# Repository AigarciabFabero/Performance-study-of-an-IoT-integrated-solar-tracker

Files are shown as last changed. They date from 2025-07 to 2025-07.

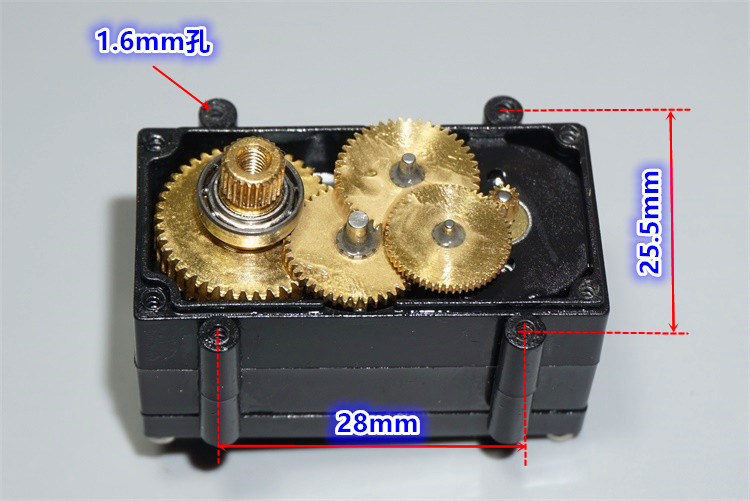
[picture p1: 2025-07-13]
Segunda_Parte/Print3D/movil/medidas/medidas3.jpg

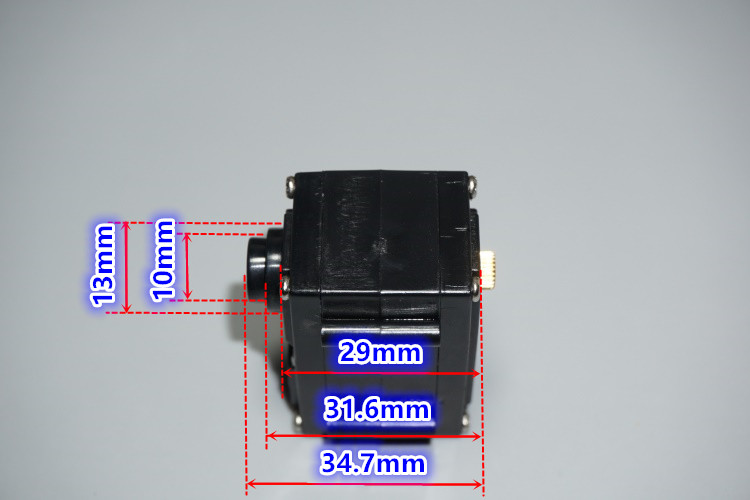
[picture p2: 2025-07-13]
Segunda_Parte/Print3D/movil/medidas/medidas1.jpg

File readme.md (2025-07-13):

# [Desarrollo y estudio del rendimiento de un seguidor solar astronómico integrado en IoT](https://dehesa.unex.es:8443/handle/10662/16877)

## Resumen

Con el objeto de mejorar la producción fotovoltaica, se pretende estudiar el rendi-
miento que se obtiene al emplear un seguidor Solar astronómico de dos ejes, respecto
a un panel fijo.
Para ello, se diseña y fabrica un prototipo constituido por dos células policristalinas
de silicio. Una de ellas sobre una estructura fija y la otra sobre un seguidor Solar
fundamentado en ecuaciones de Astrofísica y controlado por dos servomotores de tipo
bus. Además, para estudiar la mejora en la producción fotovoltaica, se diseña para
este trabajo una carga activa controlada por microcontrolador, que permite obtener el
punto de máxima potencia en todo instante.
Los datos obtenidos se suben a una plataforma de Internet de las cosas (IoT), para
su posterior estudio estadístico.
En todos los escenarios se ha podido comprobar como el seguidor Solar astronómico
de dos ejes proporciona una mejora significativa del rendimiento frente a un panel fijo
o un eje móvil.

## Abstract

The End-of-Degree Project (EDP) aims to study the improvement in photovoltaic
production achieved with a two-axis Solar tracker with respect to a fixed panel. To this
end, a prototype will be designed and built consisting of two small Solar panels, one
of them fixed and the other on a two-axis tracker controlled by bus-type servos. To
study the energy production, each panel will be connected to an active load, designed
for this work, and controlled by a microcontroller.
The data obtained will be uploaded to an Internet of Things (IoT) plataform for
forther statistical study.
In all scenarios, it has been demonstrated how the two-axis astronomical Solar
tracker provides a significant performance improvement compared to a fixed panel or
a single mobile axis.

## Prototipo final

<p align="center">
  video
</p>

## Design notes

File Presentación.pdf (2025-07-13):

### Departamento de Ingeniería Eléctrica, Electrónica y Automática

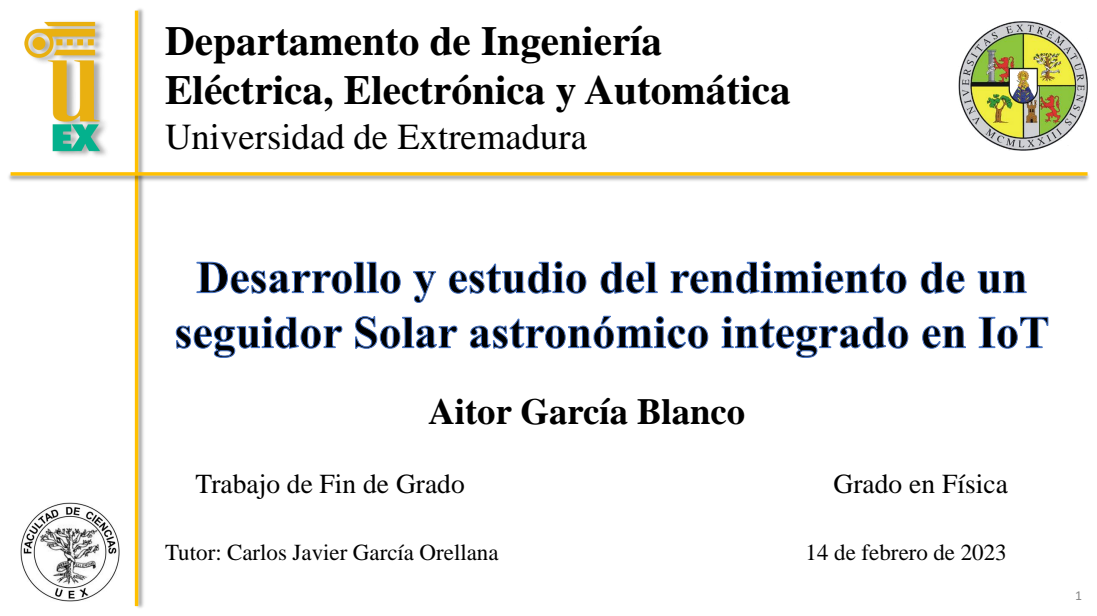
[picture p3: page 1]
Tutor: Carlos Javier García Orellana; 14 de febrero de 2023; Trabajo de Fin de Grado; Grado en Física

Universidad de Extremadura

Aitor García Blanco

## Índice

1. Introducción
2. Antecedentes
3. Materiales y desarrollo
4. Resultados ▪ Carga activa ▪ Seguidor Solar
5. Conclusiones

2

Índice

## Introducción

3

## Introducción

Con el objeto de mejorar la producción fotovoltaica, se estudia el rendimiento de un seguidor Solar astronómico de dos ejes frente a una posición fija.
- Desarrollo de una carga activa.
- Diseñar y fabricar la estructura mecánica del seguidor.
- Subir periódicamente los datos a la plataforma de “Internet of Things” (IoT).
- Analizar y estudiar los resultados obtenidos.
Introducción | 4

## Antecedentes

5

## Seguidor Solar

Estructuras móviles que pretenden maximizar la producción de electricidad en instalaciones fotovoltaicas.
➢Seguidores Solares de un único eje móvil
➢Seguidor de dos ejes móviles:
➢Control manual
➢Control automático:
➢Emplean sensores fotosensibles
➢Se fundamentan en ecuaciones astronómicas
Antecedentes | 6

## Astrofísica – Radiación Solar

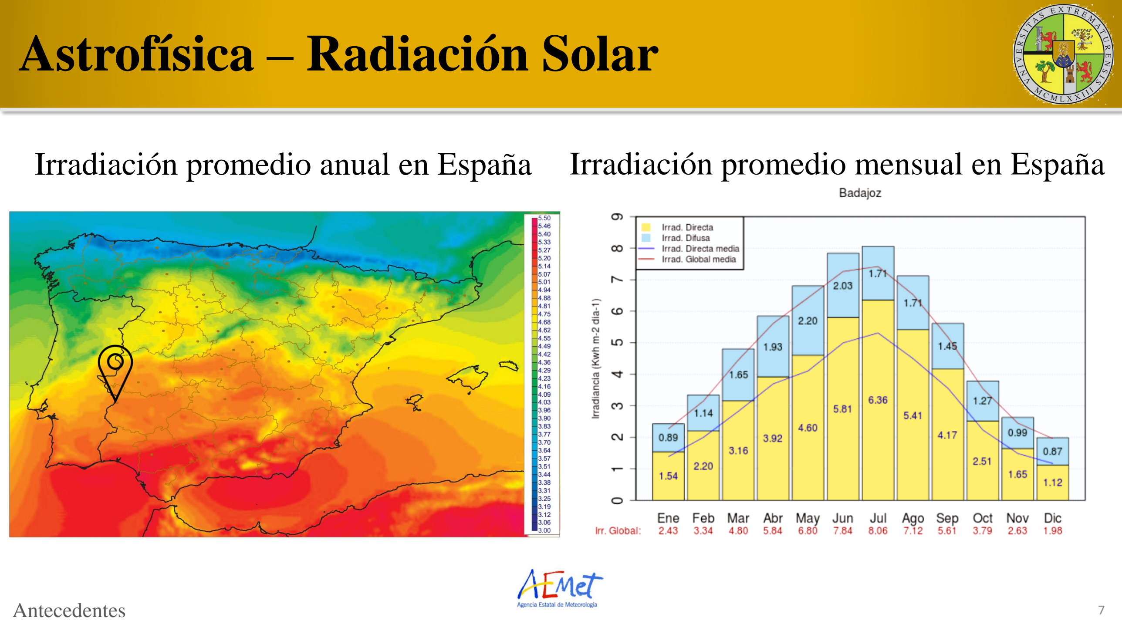
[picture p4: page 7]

Antecedentes | 7
Irradiación promedio anual en España | Irradiación promedio mensual en España

## Astrofísica – Astronomía esférica

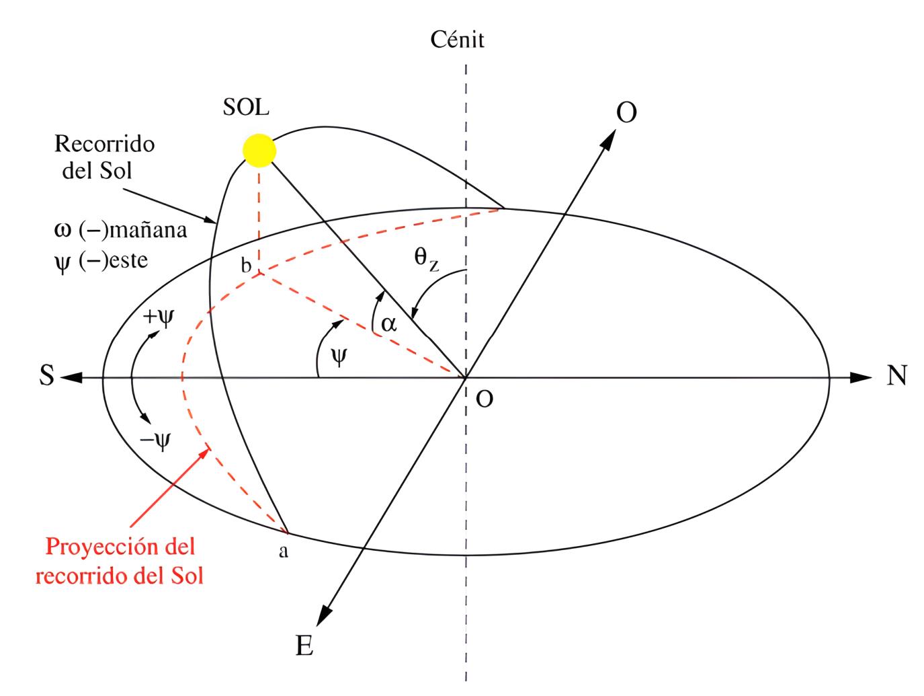
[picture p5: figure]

Antecedentes | 8

## Energía Solar fotovoltaica

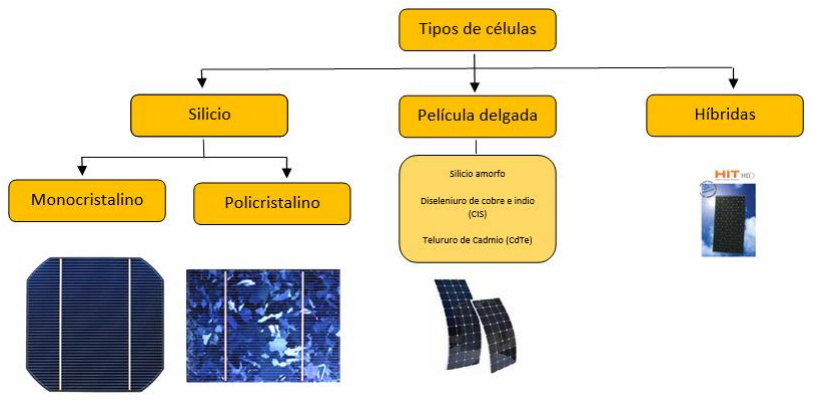
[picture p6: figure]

Antecedentes | 9

## Energía Solar fotovoltaica

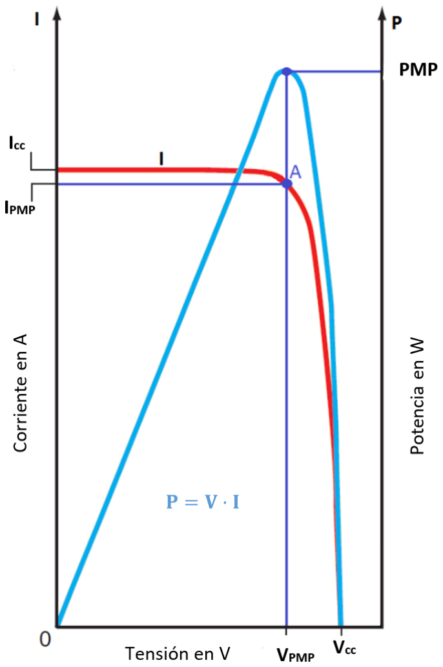
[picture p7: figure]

Antecedentes | 10

## Energía Solar fotovoltaica

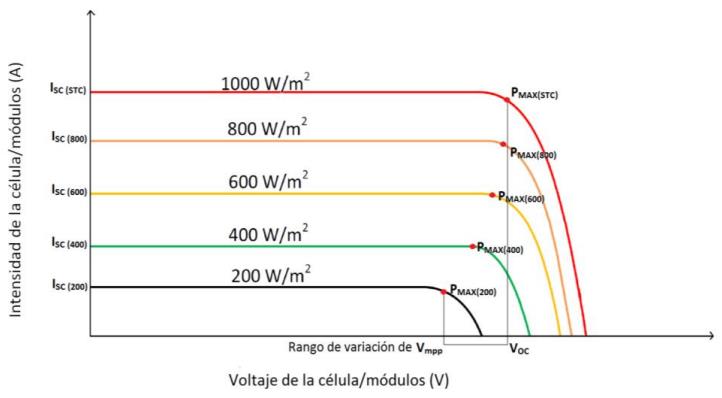
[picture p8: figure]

Antecedentes | 11

## Energía Solar fotovoltaica

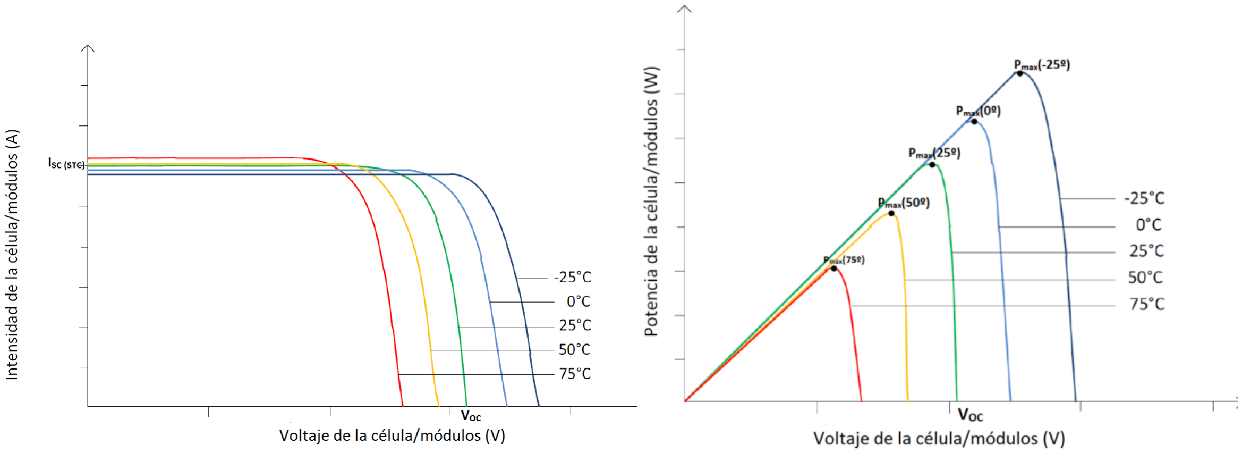
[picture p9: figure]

Antecedentes | 12

## Materiales y desarrollo

13

## Materiales

14

❑Microcontrolador ESP32

Materiales y desarrollo

❑ Células fotovoltaicas

❑ MOSFET ❑ Servomotores

❑ Conversor DC-DC

❑ Arduino IDE ❑ OpenSCAD

❑ Componentes activos y pasivos

❑ ThingSpeak

## Carga Activa - Hardware

Materiales y desarrollo | 15
- Es un dispositivo electrónico que nos permite variar la corriente que se demanda a una fuente de tensión o batería
- En este trabajo se emplea para obtener el punto de máxima potencia de la célula Solar controlando el setpoint de la corriente; siendo así, un elemento fundamental del proyecto.
- Se ha diseñado explícitamente para este trabajo

## Carga Activa - Hardware

Materiales y desarrollo | 16

## Carga activa - Hardware

17

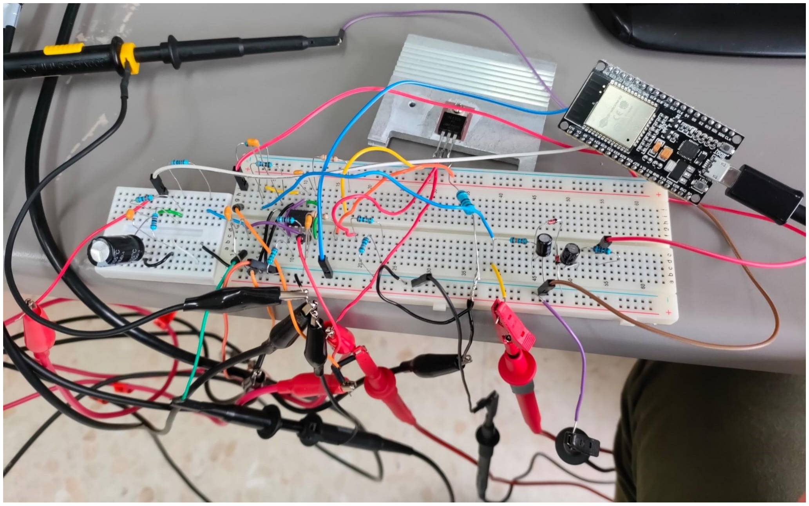
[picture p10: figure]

## Carga Activa - Software

18

- Regula la salida del DAC para mantener el setpoint para la corriente
- Incluye un lazo de control PI y un filtro de mediana para las entradas del ADC
- Para encontrar el punto de máxima potencia, el software hace un muestreo por aproximaciones sucesivas variando el setpoint de la corriente
- Una vez se encuentra el punto máximo, se repite para la otra célula fotovoltaica

Materiales y desarrollo

## Comparación rendimiento células solares

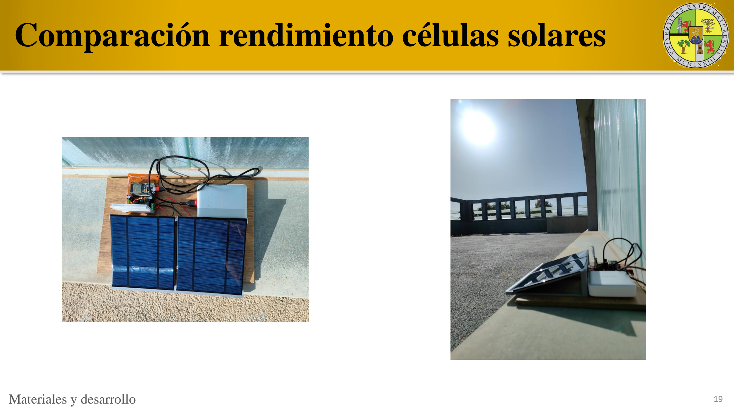
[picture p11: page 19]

Materiales y desarrollo | 19

## Comparación rendimiento células solares

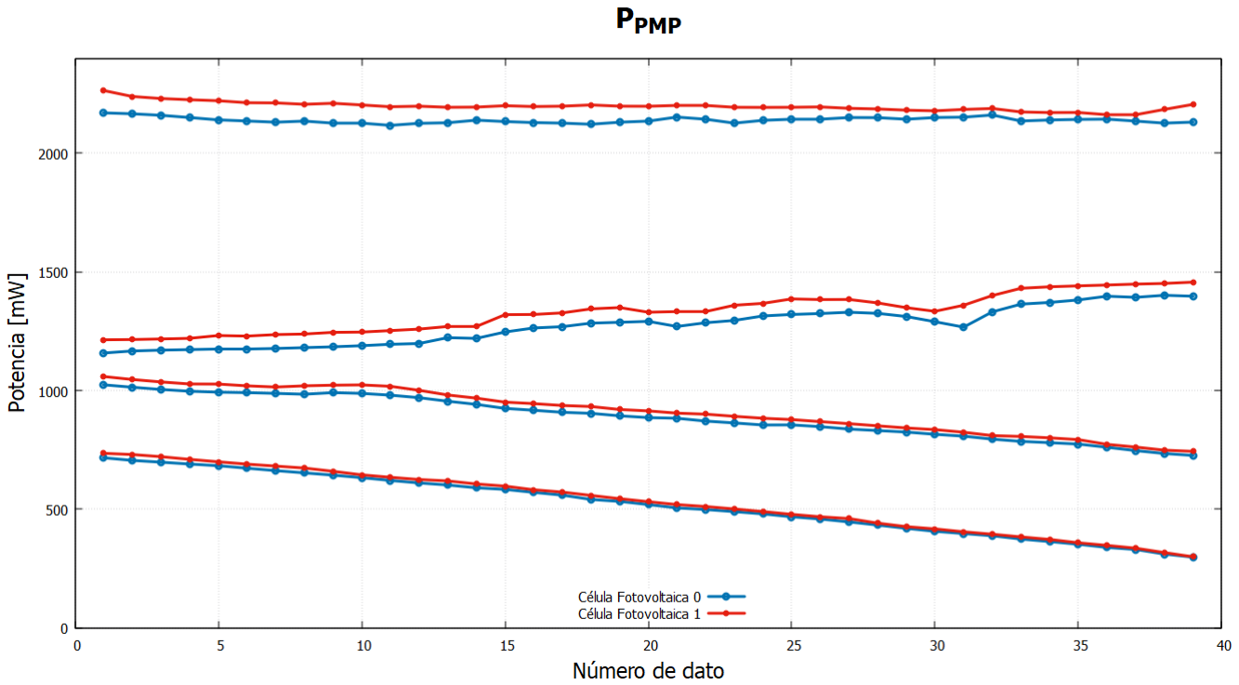
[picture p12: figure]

Materiales y desarrollo | 20

## Seguidor – Impresión 3D

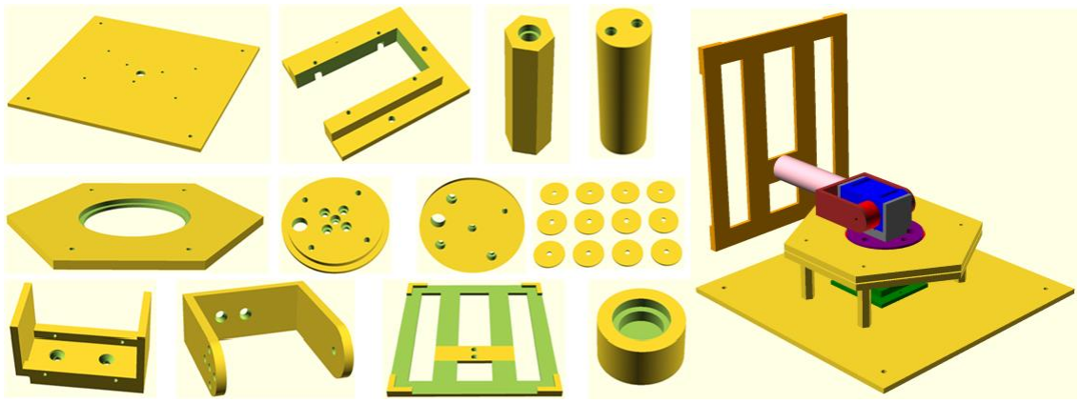
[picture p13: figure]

Materiales y desarrollo | 21

## Seguidor – Impresión 3D

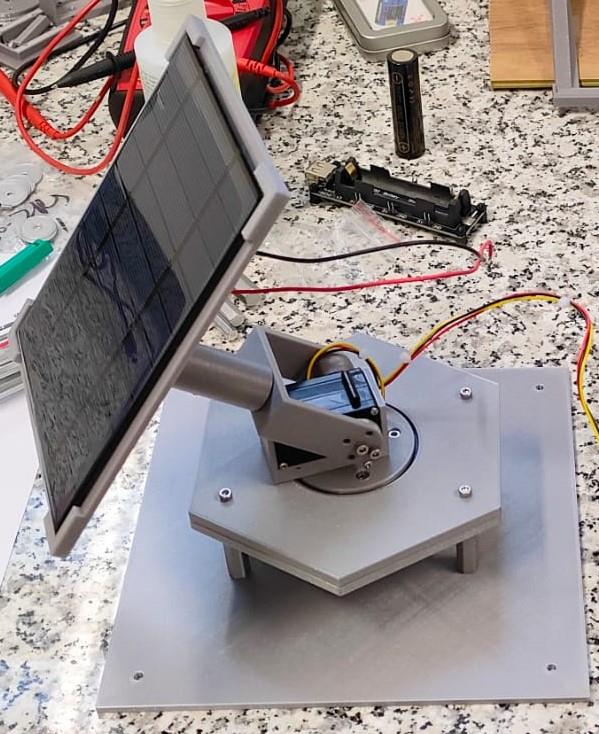
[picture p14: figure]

Materiales y desarrollo | 22

## Seguidor – Software

23

- Biblioteca de tiempos (ESP32Time) sincroniza con el servidor NTP (Network Time Protocol) , para proporciona información de tiempo en España
- Con la finalidad de obtener α y ψ, se emplean los Cálculos Generales de Posición Solar publicados por NOAA (National Oceanic and Atmospheric Administration)
- El cero del servomotor es 120 y el rango de movimiento [0-240]
- El movimiento del servo de dos ejes, tan solo tiene lugar cuando α ≥ 0

Materiales y desarrollo

## Integración

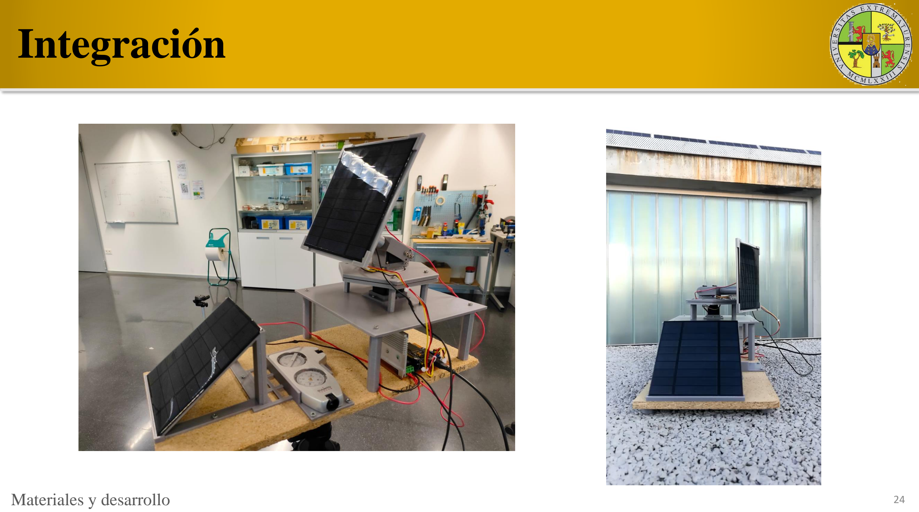
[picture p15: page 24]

Materiales y desarrollo | 24

## Integración

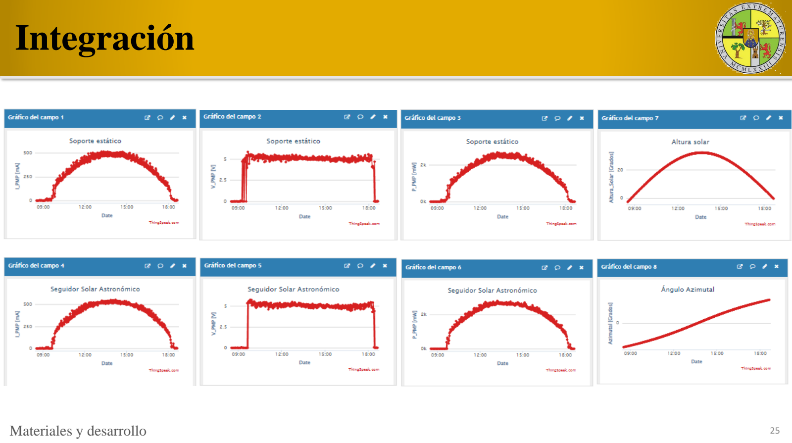
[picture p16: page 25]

Materiales y desarrollo | 25

## Resultados

26

## Carga Activa

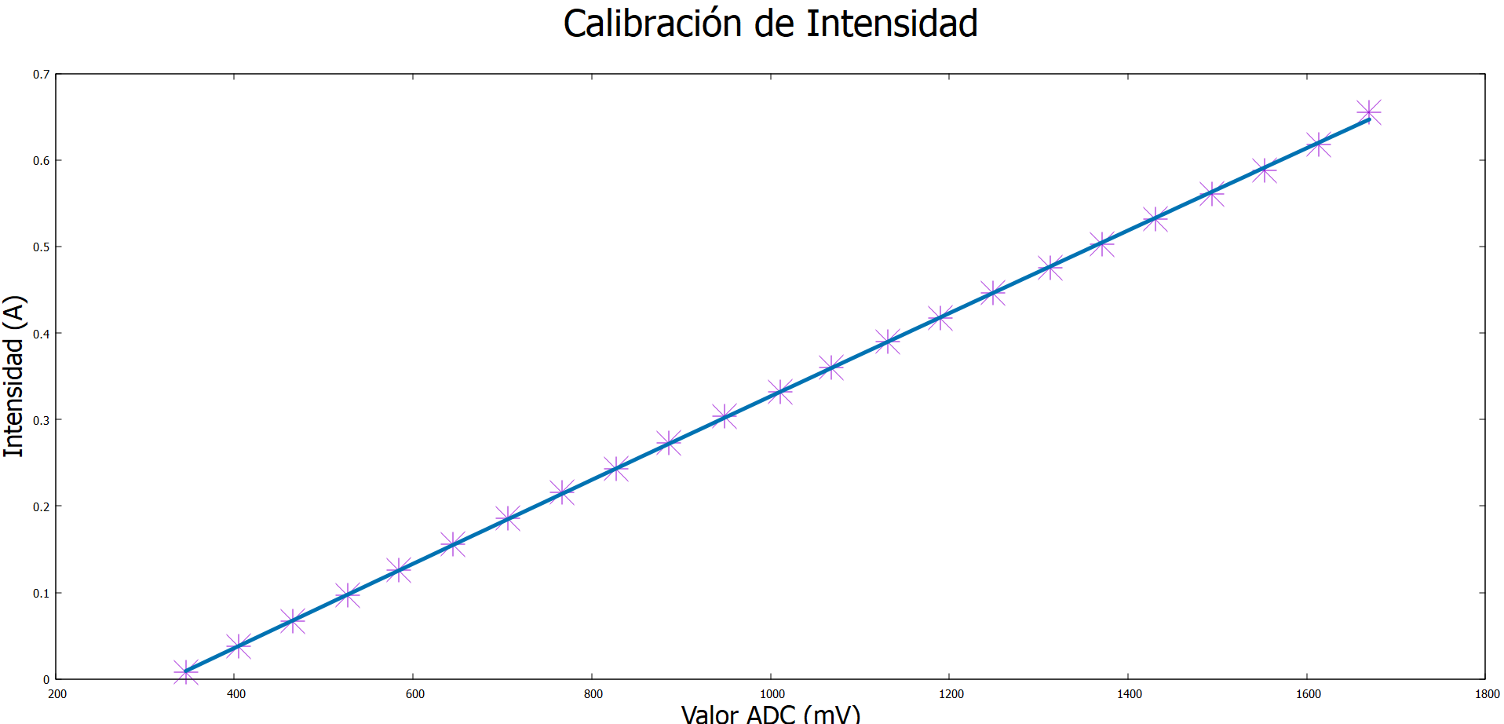
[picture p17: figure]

Resultados | 27

## Carga Activa

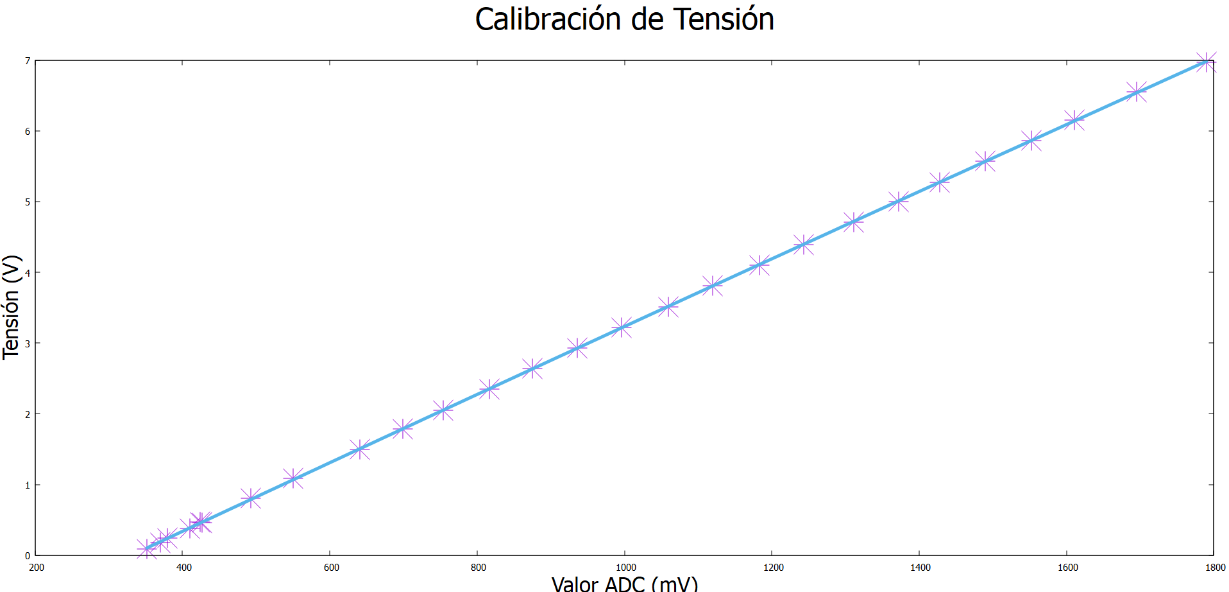
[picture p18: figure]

Resultados | 28

## Carga Activa

Resultados | 29
Calibración de la intensidad | Calibración de la tensión
a = (-5,581 ± 3,426)10⁻⁹ | a = (-5,793 ± 1,153)10⁻⁸
b = (4,933 ± 0,070)10⁻⁴ | b = (-5,581 ± 3,430)10⁻³
c = -0,160 ± 0,003 | c = -1,622 ± 0,010
R² = 0,999 | R² = 0,999

f x = ax

2 + bx + c

## Seguidor Solar

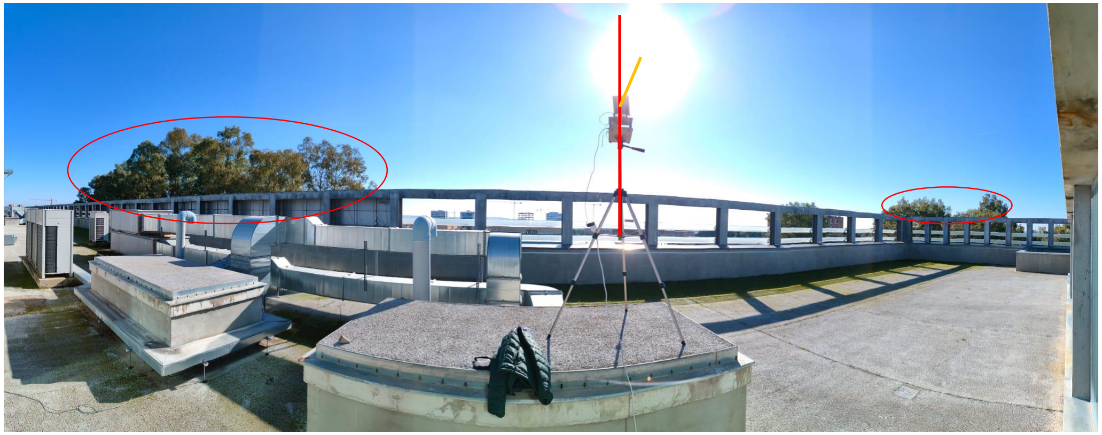
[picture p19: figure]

Resultados | 30

## Eje vertical móvil

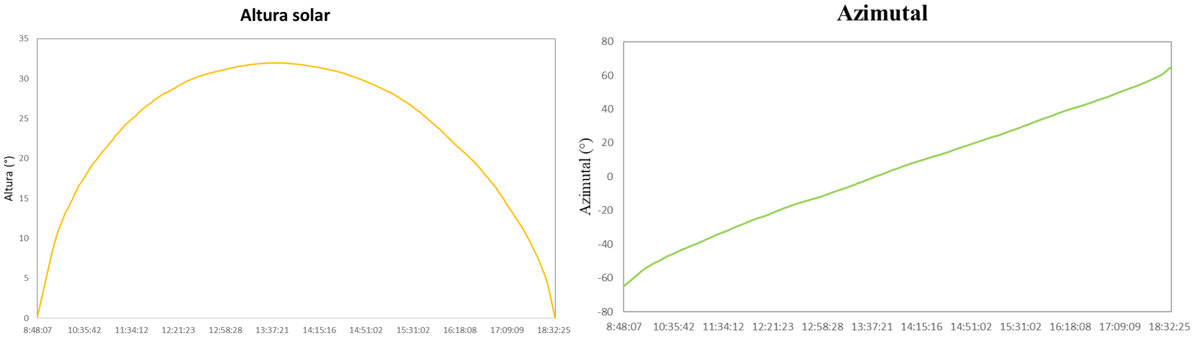
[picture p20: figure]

Resultados | 31

## Eje vertical móvil

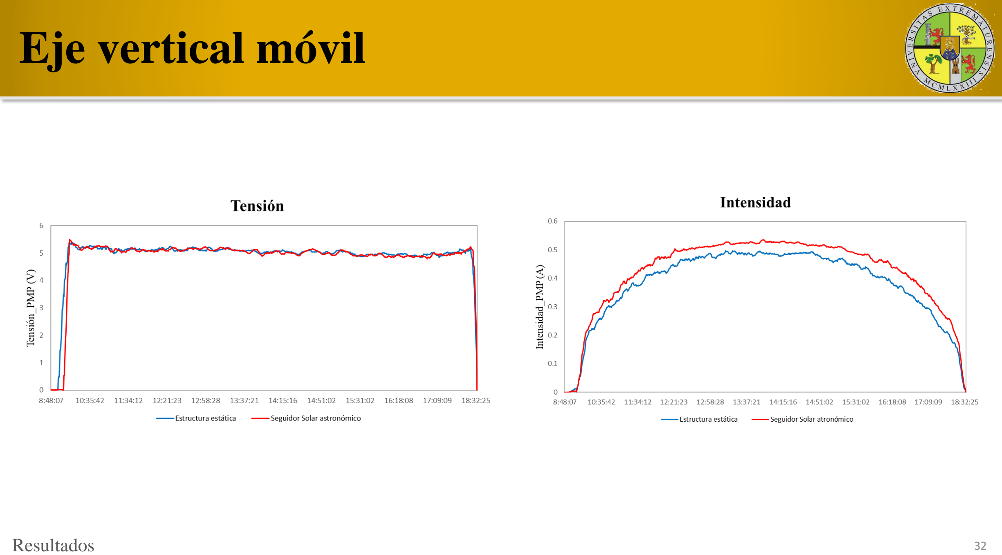
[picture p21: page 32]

Resultados | 32

## Eje vertical móvil

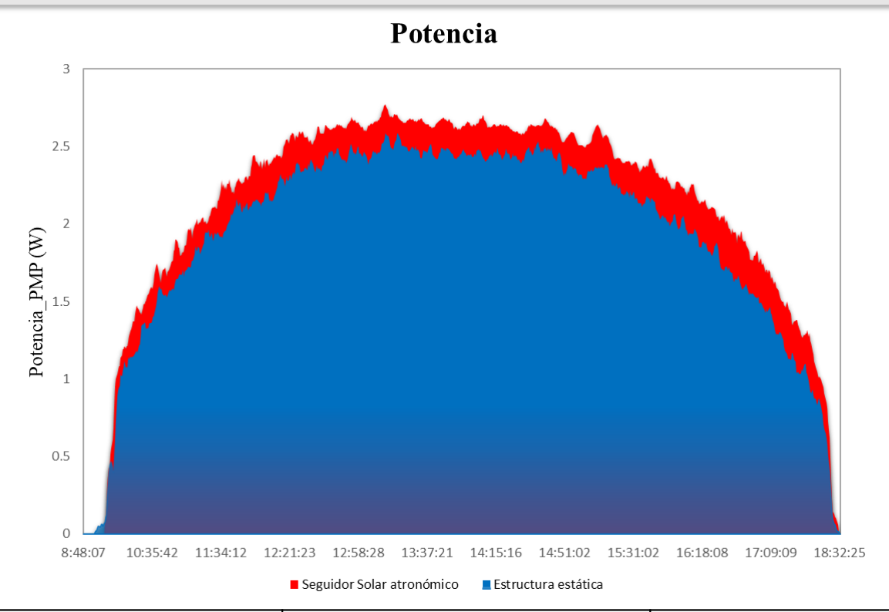
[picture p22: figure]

Resultados | 33
Energía fijo | Energía seguidor | Mejora del rendimiento
15,95 Wh | 17,71 Wh | 11,03 %

## Eje horizontal móvil

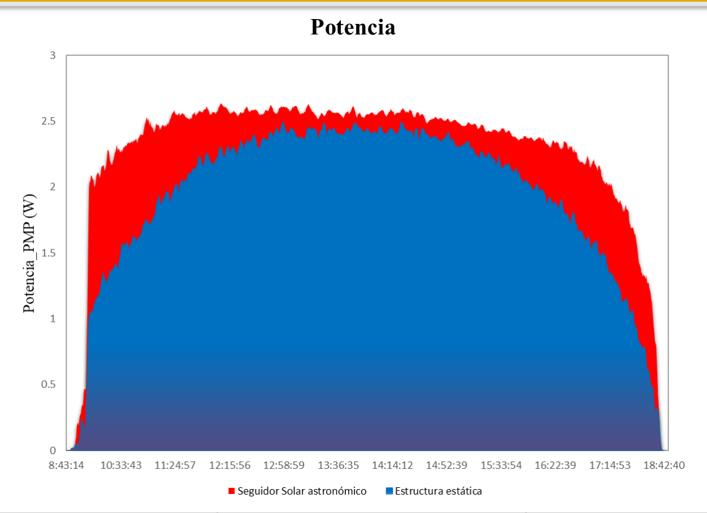
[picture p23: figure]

Resultados | 34
Energía fijo | Energía seguidor | Mejora del rendimiento
16,20 Wh | 19,90 Wh | 22,84 %

## Ambos ejes móviles

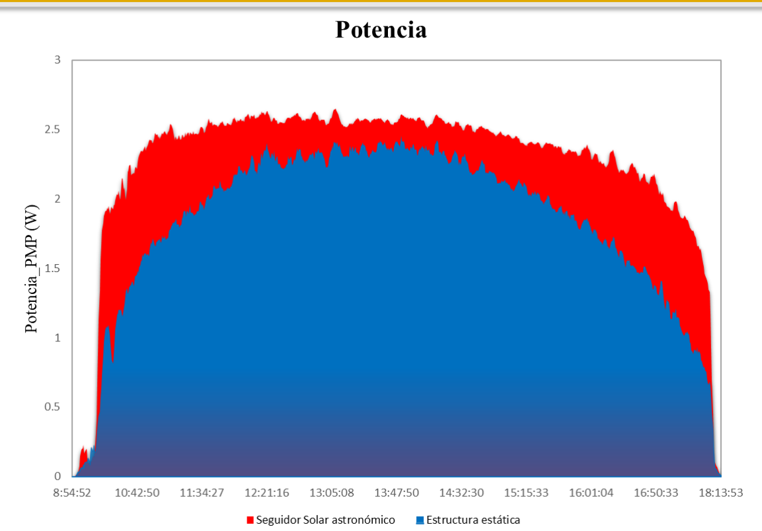
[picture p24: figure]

Resultados | 35
Energía fijo | Energía seguidor | Mejora del rendimiento
14,54 Wh | 18,46 Wh | 26,96 %

## Ambos ejes móviles

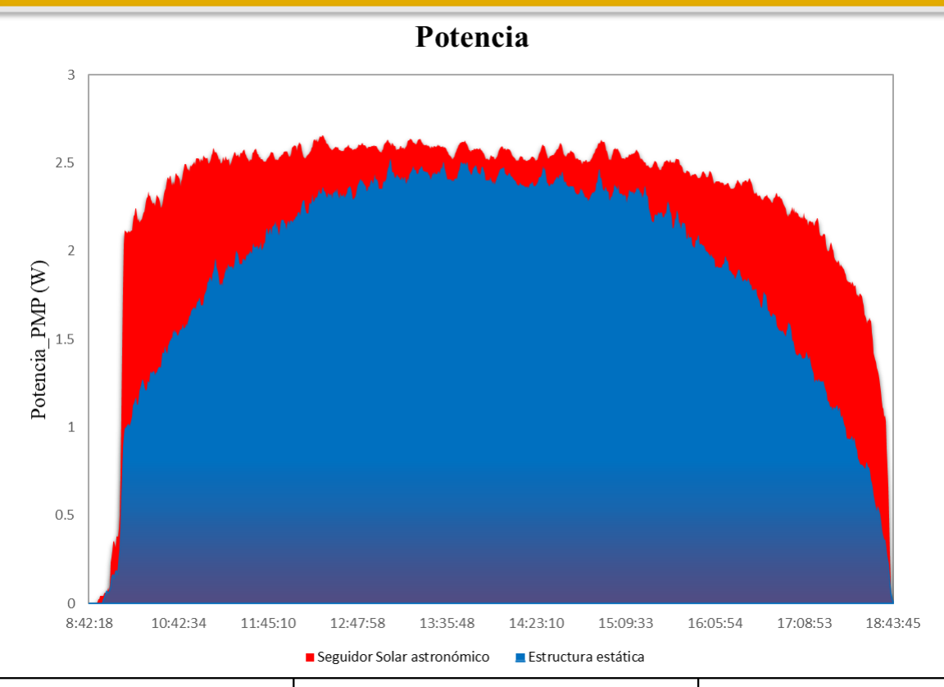
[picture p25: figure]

Resultados | 36
Energía fijo | Energía seguidor | Mejora del rendimiento
16,13 Wh | 20,48 Wh | 26,97 %

## Ambos ejes móviles

Resultados | 37
Fecha | Configuración del seguidor | Mejora del rendimiento (%)
25/01/2023 | Eje vertical móvil | 8,03
30/01/2023 | Eje horizontal móvil | 19,84
05/01/2023 | Ambos ejes móviles | 23,96
31/01/2023 | Ambos ejes móviles | 23,97

## Conclusiones

38

## Conclusiones

39

- Se ha diseñado y construido una carga activa para obtener el PMP de las células Solares
- Se ha diseñado y construido un seguidor Solar de dos ejes mediante impresión 3D y servomotores
- El seguidor Solar de doble eje es la configuración con mejor rendimiento
- El seguidor Solar es muy útil para espacios reducidos
- Se espera que los resultados mejoren significativamente para los meses de verano

Conclusiones

### Departamento de Ingeniería Eléctrica, Electrónica y Automática

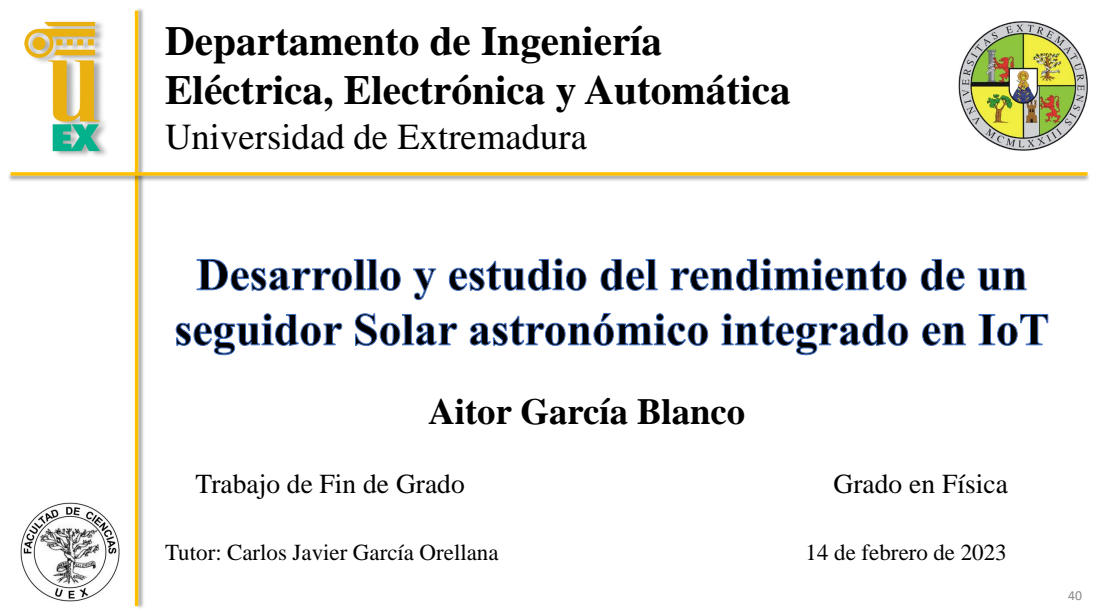
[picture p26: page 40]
Tutor: Carlos Javier García Orellana; 14 de febrero de 2023; Trabajo de Fin de Grado; Grado en Física

Universidad de Extremadura

Aitor García Blanco

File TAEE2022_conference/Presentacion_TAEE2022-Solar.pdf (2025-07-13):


## Estudio del rendimiento de un seguidor solar integrado en IoT

A. García Blanco, C. J. García Orellana, E. Abengózar García-Moreno

Teruel, Junio de 2022
TAEE 2022

Departamento de Ingeniería Eléctrica, Electrónica y Automática Universidad de Extremadura

Universidad de Extremadura; Contenidos

Estudio del rendimiento de un seguidor solar.


TAEE 2022. | 2 de 20

Dpto. Ing. Eléctrica,
Electrónica y Automática.

Introducción.
Desarrollo del TFG.
Plan de trabajo.
Carga activa.
Resultados actuales.
Conclusiones.

Contenidos

TAEE 2022. | 3 de 20

Introducción.
Desarrollo del TFG.
Plan de trabajo.
Carga activa.
Resultados actuales.
Conclusiones.

Contenidos

Universidad de Extremadura | Introducción y objetivos

¿Qué se pretende hacer?
Estudiar la mejora en la producción fotovoltaica con un seguidor solar. Comparar la producción de dos paneles (fijo y montado en un seguidor). ¿Cómo se aborda?
Se estudia la energía producida con una carga activa diseñada en este trabajo.

Introducción

TAEE 2022. Introducción.; Los datos obtenidos se subirán a una plataforma IoT para su análisis.


TAEE 2022. Objetivos. | 5 de 20
Universidad de Extremadura | Introducción y objetivos

Reforzar las competencias del ámbito académico.
Abordar los siguientes objetivos específicos:

Diseñar y fabricar el sistema mecánico y de control del seguidor.
Medir de forma precisa la capacidad de producción de energía de cada uno de los dos paneles solares mediante una carga activa.
Subir datos a una plataforma IoT.
Comparar los rendimientos obtenidos.

Objetivos

TAEE 2022. | 6 de 20

Introducción.
Desarrollo del TFG.
Plan de trabajo.
Carga activa.
Resultados actuales.
Conclusiones.

Contenidos

Desarrollo y test de la carga activa; Diseño y fabricación de la estructura; Toma de datos; Memoria del TFG

TAEE 2022. Desarrollo del TFG. | 7 de 20
Universidad de Extremadura | Plan de Trabajo

Desarrollo y test de la carga activa.
Diseño y fabricación de la estructura y sistema de control del seguidor. Toma y análisis de datos.
Memoria del TFG.

Plan de Trabajo

Universidad de Extremadura | Carga activa. Elementos

Encargado de controlar la carga activa y los servomotores del seguidor.
Algunas especificaciones:

520 KBytes de memoria SRAM y 448 Kbytes de ROM. Hasta 16 MBytes de memoria Flash externa por SPI.
Tensión de trabajo entre 3.0 y 3.6 V.
Frecuencia de operación de hasta 240 MHz.
Varios periféricos integrados en el chip: contadores, generadores PWM, buses I2C y SPI, etc.
Varios ADC de hasta 12 bits y dos salidas DAC de 8 bits.
Comunicaciones WiFi y Bluetooth.

Microcontrolador ESP32 (Espressif)

Universidad de Extremadura; Carga activa. Elementos

Microcontrolador ESP32. ADC y DAC

ADC: Vref~1.1 V, pero con atenuador 6dB, obtenemos un rango lineal
de 150 mV - 1.75 V → Necesidad de desplazamiento de la señal.

DAC: Rango de salida 150 mV - 3.2 V → Necesidad de desplazamiento
de la señal.

Ciertamente, los
ADC y DAC del
ESP32, tienen
sus pegas.


Universidad de Extremadura | Carga activa. Esquema

MOSFET controlado mediante muestreo de corriente, formando una fuente de corriente, con el setpoint dado por una tensión de control.
El microcontrolador varía la corriente que demanda la carga activa, mide la tensión y corriente del panel, y obtiene la potencia máxima.

Carga activa

Universidad de Extremadura; Carga activa. Detalles; Setpoint; I setpoint=; V setpoint R5

Carga activa. Fuente controlada de corriente.
Esquema de realimentación de corriente en serie.

Conexión al panel
solar

amplificador operacional realimentado
U1A controla el MOSFET Q1
corriente al valor del setpoint fijado por
la tensión en la entrada no inversora de

muestrea la corriente y el

para llevar la

Medida de la corriente
del panel

entonces; Vout; R2R3Vref R1R3+R2 R3+R2R1; R2 R3Vref R1; Necesitamos tres desplazadores.

Carga activa. Detalles

Universidad de Extremadura
Carga activa. Desplazadores y adaptadores de nivel.
Para solucionar los problemas con rango inferior de los ADC y DAC del
ESP32 usamos desplazadores / adaptadores.

Universidad de Extremadura; Carga activa. Detalles; Vin→0.15 … 3.3 V y Vout→0 … 0.35 V

Carga activa. Desplazadores y adaptadores de nivel.

Adaptador corriente panel (ADC2)

Vin→0 … 3.3 V y Vout→0.3 … 1.7 V
Adaptador tensión panel (ADC1)

Vin→0 … 7 V y Vout→0.3 … 1.8 V
Adaptador de control (DAC)

Necesita una
tensión de referencia
negativa.

Universidad de Extremadura | Carga activa. Detalles

Necesitamos una tensión negativa para poder ajustar el desplazamiento de la tensión del DAC. Consideraciones:

Valor exacto no es importante.
Corriente del orden de microamperios.
Solución: Oscilador + restaurador + rectificador de media onda.

Carga activa. Generador de tensión negativa


Universidad de Extremadura | Carga activa. Software

En la medida de los ADC se utilizar un filtro de mediana.
Una parte se encarga de controlar la salida del DAC para mantener el setpoint seleccionado para la corriente.
Se implementa mediante un lazo de control PI.

Búsqueda de punto de máxima potencia mediante muestreo por aproximaciones sucesivas.
El proceso se repite para el otro panel.
Los datos se suben a ThingSpeak.

Carga activa. Software de control.


Universidad de Extremadura | Carga activa. Montaje

Carga activa. Montaje.


TAEE 2022. Resultados actuales. | 17 de 20
Universidad de Extremadura | Resultados actuales

Calibración de las dos entradas ADC (tensión y corriente). Las regresiones cuadráticas se ajustan mejor (error correlación < 1%).

Resultados actuales

Evaluación de la carga activa y el software con una fuente de laboratorio en lugar del panel solar.
Se espera obtener mayor producción en el panel del seguidor, aunque habría que considerar el consumo de los actuadores para ver el rendimiento global.

TAEE 2022. | 18 de 20

Introducción.
Desarrollo del TFG.
Plan de trabajo.
Carga activa.
Resultados actuales.
Conclusiones.

Contenidos

TAEE 2022. Conclusiones. | 19 de 20
Universidad de Extremadura | Conclusiones

Se ha diseñado e implementado un circuito de carga activa controlado por microcontrolador para la medición de la producción de los paneles solares.
El uso de los ADC y DAC del ESP32 ha complicado el circuito final
Se han realizados pruebas de laboratorio de la carga activa mediante una fuente controlada.
Se han conseguido realizar las calibraciones de los ADC y DAC correctamente.
El trabajo continúa con el desarrollo de la plataforma del seguidor.

Conclusiones

## Preguntas y Agradecimientos

TAEE 2022. Preguntas y Agradecimientos.; Universidad de Extremadura; Preguntas y Agradecimientos

¿Preguntas, dudas?
Agradecimientos
Este trabajo ha sido financiado por la Junta de Extremadura a
través de la Ayuda GR21087, parcialmente financiada por FEDER.

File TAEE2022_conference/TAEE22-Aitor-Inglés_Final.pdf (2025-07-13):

# Performance study of an IoT-integrated solar tracker

Aitor Garc´ıa-Blanco
Dpto. de Ing. Electrica, Electr ´ | onica y Autom ´ | atica ´
Universidad de Extremadura Badajoz - SPAIN
Email: aigarciab@alumnos.unex.es

Carlos J. Garc´ıa-Orellana
Dpto. de Ing. Electrica, Electr ´ | onica y Autom ´ | atica ´
Instituto de Computacion Cient ´ | ´ıfica Avanzada (ICCAEx)
Universidad de Extremadura Badajoz - SPAIN
Email: cjgarcia@unex.es
Eugenio Abengozar-Garc ´ | ´ıa
Dpto. de Ing. Electrica, Electr ´ | onica y Autom ´ | atica ´
Instituto de Computacion Cient ´ | ´ıfica Avanzada (ICCAEx)
Universidad de Extremadura Badajoz - SPAIN
Email: euabga04@alumnos.unex.es

Abstract—The End-of-Degree Project (EDP) aims to study the improvement in photovoltaic production achieved with a two-axis solar tracker with respect to a fixed panel. To this end, a prototype will be designed and built consisting of two small solar panels, one of them fixed and the other on a two-axis tracker controlled by bus-type servos. To study the energy production, each panel will be connected to an active load, designed for this work, and controlled by a microcontroller. The data obtained will be uploaded to an Internet of Things (IoT) platform. Index Terms—Solar tracker, IoT, active load, photovoltaic panel, photovoltaic performance.

I. OBJECTIVE OF THE EDP AND WORK PLAN
The End-of-Degree Project (EDP) is currently part of all Bachelor’s Degree studies. In general, it is one more subject in which the student must demonstrate the acquisition of the degree competences through the development of an autonomous but supervised work. In scientific studies, the EDP is something new and sometimes it is given an excessively research-oriented character, being confused with dissertations after the old Undergraduate Degrees.
The End-of-Degree Project, of which we present its objectives, planning and partial development, is part of the Bachelor’s Degree in Physics at the University of Extremadura. In the Degree in Physics syllabus [1], the EDP is assigned 6 ECTS credits and the Teaching Plan [2] states that “the EDP aims for the student of the Degree in Physics to develop with autonomy the knowledge and skills acquired to carry out work related to this degree, thus demonstrating that they have achieved the competences foreseen in their syllabus”. The competences of the Bachelor’s Degree in Physics focus on the student acquiring a basic training in addressing and solving problems, with a critical spirit and creativity, related to the field of Physics and Science, although not only. Emphasis is also placed on the knowledge of experimental techniques and methodologies. Students on the Bachelor’s Degree in Physics take two compulsory subjects in Analogue and Digital Electronics and can take an optional subject in Semiconductor Devices.
Therefore, in relation to the proposed EDP, the student has knowledge of Analogue and Digital Electronics (including microcontrollers and FPGAs), as well as knowledge of Astrophysics (they have taken one subject) and several experimental methods.
A. Objectives of the EDP
The proposed EDP has objectives in two areas. On the one hand, the objectives related to the competences of the degree and, on the other hand, the specific objectives of the work to be carried out.

Competence-related objectives:

The proposed EDP not only addresses the design of an electronic system for a specific application, but mainly aims to enable the student to put into practice the skills to be acquired with the degree [1]. Specifically, the student is expected to work on the following areas:
- The aim is to enhance the knowledge of Analogue and Digital Electronics, in particular in microcontrollers and rapid prototyping systems.
- To introduce students to wireless communication systems and the Internet of Things (IoT), based on previously acquired knowledge.
- Apply the skills acquired in Astrophysics to track the position of the sun.
- To develop the general competences linked to the preparation and presentation of the dissertation.

Objectives of the work:

The main objective of the EDP is to study the performance of a two-axis solar tracker, with respect to a solar panel in a
978-1-6654-2161-4/22/$31.00 © 2022 IEEE | fixed position, in a rigorous and systematic way.

To this end, the following specific objectives must be addressed:
- Design and build the mechanical system of the tracker, consisting of a structure (made with 3D printing) and bus-type servomotors. A microcontroller-based system will be used to carry out the tracking, using the physical equations of solar tracking to find the best incidence of solar radiation at all times.
- To measure precisely the energy production capacity of each of the two solar panels (the one mounted on the tracker and the fixed one). To do this, we propose using an active load, controlled by a microcontroller, which seeks the maximum power point of each panel at any given moment.
- Upload periodically the maximum power of each panel to an Internet of Things (IoT) platform, facilitating data capture.
B. Work Plan
The work plan initially proposed divides the development of the EDP into four parts, the first two sequentially and the last two in parallel. These parts are as follows:
1) Development and testing of the active load. This is undoubtedly the part of the EDP with the most electronic content, both analogue and digital. The design, assembly as a prototype and final assembly will be carried out, as well as the corresponding testing. The software for its integration in IoT will also be developed.
2) Design and build of the structure of the tracker. The structure to house the tracker and the fixed solar panel will be designed and manufactured using 3D printing. Software will be developed to guide the solar tracker according to the solar position.
3) Data collection. Once the complete system has been set up, data will be collected for several days in order to obtain statistically significant results.
4) Final dissertation report. Considering that the previous phase will be relatively unattended, the writing of the final dissertation report will be started in parallel with it.

II. CURRENT DEVELOPMENT
In this section we will describe in general the current development of the EDP, explaining the most relevant parts of it.
A. Global description
The overall aim of the system to be designed and built is to study the performance improvement of a solar panel when it is mounted on a solar tracker, compared to one that remains fixed, with the most favourable orientation. To do this, we will move the tracker according to the equations of solar movement (depending on the GPS position of our system) and at each step of the movement we will look for the maximum electrical power that we can extract from each of the two panels.

To obtain this maximum power we will use an active load controlled by a microcontroller, which we will switch between the two panels. This active load will be designed and assembled as part of the EDP, based on one of the existing designs [3], and will upload the measurements obtained to an IoT platform. In order to find the maximum power, the microcontroller will vary the current demanded by the active load (setpoint), performing a sweep and will measure the voltage of the panel under study, obtaining at the end of the sweep the maximum power that can be extracted from the panel in question.
The solar panels chosen for the work have a size of 13x15 cm, with 3 W power and VOC of 6.1 V and an ISC of 600 mA, therefore these values are the work limits of our active load.
B. ESP32 microcontroller
The microcontroller is one of the fundamental elements used in the EDP, as it will be in charge of controlling the active load and the movement of the servomotors that will carry out the tracking.
The chosen microcontroller is the ESP32 microcontroller from Espressif. It is a 32 bits microcontroller, with WiFi and enough power. The detailed specifications can be found at [4], the most important ones being the following:
- Has 520 KBytes of SRAM memory and 448 KBytes of ROM.
- Up to 16 MBytes of external Flash memory through SPI, mappable in the read-only area.
- The operating voltage is between 3.0 and 3.6 V.
- The operating frequency is up to 240 MHz.
- It includes several peripherals integrated in the chip: counters, PWM generators, I2C and SPI buses, etc.
- It has several ADCs of up to 12 bits and two 8-bit DAC outputs.
- WiFi and Bluetooth communications.
The microcontroller itself has no flash memory, so it is normally distributed as a module that includes this memory, as well as the clock and the antenna. In our case we have used the module mounted on a development board.
For the choice of this microcontroller we have taken into account its connectivity (it has WiFi) and its ADC and DAC converters. However, we have encountered some problems when working with the converters.
On the one hand, the ADC converters (SAR type) have a reference voltage of around 1.1 V (the specific value is stored internally and can be read), so they incorporate a programmable attenuator at the input. In our case, we have selected an attenuation of 6 dB, which gives us an effective working range for the ADC inputs of between 150 mV and 1.75 V [5], which requires a signal shift in the signal adaptation stage to enter into the ADC working range. In addition, to improve linearity we have lowered the resolution to 11 bits.
On the other hand, in the DAC we have a similar problem. Its range is approximately from 150 mV to 3.2 V, so we also have to shift the signal, but now downwards, in order to properly control the active load and to obtain sufficiently low currents. In this case, linearity is not so important.
The software development has been done using the Arduino development environment [6], which perfectly supports the ESP32 microcontroller. Arduino, with its C-based syntax, is a simple and convenient environment for the development of this type of rapid prototyping applications, despite its possible limitations.
C. Active load
The design and assembly of the active load is one of the fundamental parts of the work. Its development allows the student to improve his skills in Analogue and Digital Electronics.
The active load has a MOSFET controlled by a currentsampling feedback amplifier, forming a current source whose value will be determined by a control voltage. A DAC and an ADC of the microcontroller will be used to control the current absorbed by the active load. The voltage of the solar panel will also be measured (with another ADC) in order to calculate the power available at any given moment.
The design of each of the blocks has been carried out using the LTSpice [7] simulator, performing the complete simulation to verify its correct operation, including the model of the solar panel.
The complete scheme of the active load can be seen in Fig. 1, in which we have highlighted the different functional blocks, which we will describe in more detail below.

Controlled current source:
The controlled current source is one of the central parts of our design. As we can see in Fig. 1 its fundamental elements are the MOSFET transistor Q1, the resistor R5 and the operational amplifier U1A. The scheme corresponds to that commonly used for a voltage-controlled current source, using a feedback scheme of series current [8]. Resistor R5 samples the current and through the feedback loop the operational amplifier U1A controls the MOSFET Q1 to bring the current to the reference value (setpoint), set by the voltage present at the non-inverting input of U1A, according to the expression 1.

Isetpoint =

Vsetpoint
R5

(1)

If we consider that the active load must work in the range of 0 to 700 mA, we have that the control voltage at the non-inverting input of U1A must be between 0 and 350 mV. With regards to the characteristics of the components, we should point out that Q1 must have a threshold voltage of around 2 V (we work with a 3.3 V supply), U1A must be of the rail-to-rail type and R5 must have a tolerance of 1 %.

Shifters and level adapters:
As previously mentioned, the problems with the lower range of the ESP32’s ADCs and DAC force us to shift our signals to get into the proper operating ranges.
We have used for the displacement and the necessary attenuation the circuit that can be seen in Fig. 2. If we analyse the circuit, the relationship between the output and the input is given by the expression 2.

Vout =

R2R1
R1R3 + R2R3 + R2R1

Vin+

R2R3Vref
R1R3 + R2R3 + R2R1

(2)

If the condition R1 R2 and R1 R3 are met, then the expression 2 can be approximated by the expression 3, in which we can see that the circuit acts approximately as a voltage divider plus a shift. The sign of this displacement depends on the sign of Vref .

Vout ≈

R2
R3 + R2

Vin +

R2R3Vref
R1(R3 + R2)

(3)

As it can be seen in the global scheme (Fig. 1), we have used three of these circuits to adapt the signals, two of them with a positive displacement (for the ADC inputs of the microcontroller) and the other with a negative displacement (for the DAC output), specifically:
- Panel current adapter (ADC2):
Vin → 0 . . . 3, 3 V y Vout → 0, 3 . . . 1, 7 V
- Panel voltage adapter (ADC1):
Vin → 0 . . . 7 V y Vout → 0, 3 . . . 1, 8 V
- Control adapter (DAC):
Vin → 0, 15 . . . 3, 3 V y Vout → 0 . . . 0, 35 V

Negative voltage source:
As mentioned above, we need negative voltage in order to adjust the voltage offset of the DAC. The exact value of this voltage is not very important and the current we need is in the order of microamperes. We have therefore decided to generate it using an oscillator, a restorer [9] and a half-wave rectifier. For the oscillator we have used a PWM output of the microncontroller itself, obtaining a negative reference voltage of about -2.3 V.

Solar panel selector:

Since we want to compare the measurements of two solar panels (fixed and mounted on the tracker), we must either use two active loads or switch an active load between the two panels. We have chosen the second option, as this limits the number of components used and the time required for the measurement allows us to do this without any problems. For this we have used a simple relay, activated by means of a transistor, as shown in Fig. 1.

Control software:
The active load control software is responsible for regulating the DAC output to maintain the selected setpoint for the current. This software includes a PI control loop and a median filter for the ADC inputs, the actuation is performed directly on the DAC.
To find the point of maximum power, the control software makes a sampling, by successive approximations, varying the setpoint of the current.

10n R8

# 39K GND


Fig. 1. Overall scheme of the active load and its control.

Fig. 2. Schematic diagram of the circuit used to shift and adapt the signals.

Fig. 3. Assembly of the active load on the protoboard.

Once the maximum point is found, the process is repeated
for the other solar panel and the results are uploaded to the
IoT platform ThingSpeak [10], which is the one we have
finally chosen. The decision to use this platform is due to
the simplicity with which it can be used from the Arduino
environment.

movement of the tracker we will use bus type servomotors,
controlled from the ESP32 microcontroller.
Once the design has been finalised, we will make the
designed parts using 3D printing. In order to evaluate possible
manufacturing differences between the two solar panels, we
will make two fixed supports to compare their performance.

In Fig. 3 we can see the initial assembly on the protoboard
for the test and adjustment of the components and in Fig. 4
the final assembly using a standard dot PCB.

III. PRESENT AND EXPECTED RESULTS

D. Solar tracker platform and solar panels
The current development of the EDP now focuses on the
design of the parts to mount the fixed panel with the appropri-
ate inclination and on the design of the tracker itself. For the

Regarding the results, on the one hand, we have calibrated
the two ADC inputs of the ESP32 with respect to the voltage
and current in the active load. In both cases we have performed
linear and quadratic regressions, obtaining better results with


Fig. 4. Assembly of the active load on the PCB.

Current calibration; ADC Value (mV); Current (A)

I(A) = − 5,58E-09 ADC² + 492,74E-06 ADC − 160,48E-03

Fig. 5. ESP32 ADC calibration results used to measure the current flowing through the load.

the latter. We can see in Fig. 5 the fit for the intensity and in Fig. 6 for the input voltage. In both cases the correlation coefficient is excellent and the data show an error of less than 1% over practically the whole range, except at the extremes, especially for very low currents.
On the other hand, we have evaluated in the laboratory the performance of the active load by varying the current demanded at the setpoint, using a laboratory source instead of the solar panel. These initial results are very satisfactory, obtaining a coherent and fast response of the active load to changes in the current setpoint.
Regarding the overall results of the EDP, we expect the solar tracker to obtain a higher energy production than the

Voltage calibration; ADC Value (mV); Voltage (V)

V(V) = − 59,64E-09 ADC² + 4,91E-03 ADC − 1,62E+00

Fig. 6. Results of the ESP32 ADC calibration used to measure the input voltage to the load.

fixed panel [11]. Although some authors obtain contrary results when considering the consumption of the actuators, especially in equatorial areas [12]. In this way, we will be able to establish the margin of energy available to power the actuators and their control electronics.

ACKNOWLEDGEMENTS
This work has been partially funded by the Junta de Extremadura and ERDF through the research group grant GR21087.

REFERENCES

[1] Verified memory of the Degree in Physics. https://www.unex.es/organizacion/gobierno/vicerrectorados/vicecal/archivos/ficheros/informacion-titulos/ciencias/plan0140/memoriaplan.pdf
[2] Syllabuses of the Faculty of Science (UEX). https://www.unex.es/conoce-la-uex/centros/eii/informacion-academica/programas-asignaturas.
[3] Hessling, Andre. Active load with microcontroller - Part 1- ´
6. | Andres | Blog, | 2016. | https://andrehessling.de/2016/02/07/ ´
project-active-load-with-microcontroller-part-1-requirements/
[4] Espressif Systems. ESP32 Series Datasheet, 2022. https://www.espressif.com/sites/default/files/documentation/esp32 datasheet en.pdf
[5] Espressif | Systems. | ESP32 | Analog | to | Digital | Converter.
https://docs.espressif.com/projects/esp-idf/en/latest/esp32/api-reference/peripherals/adc.html
[6] Website of the Arduino project. http://www.arduino.cc.
[7] Analog | Devices. | LTSpice | simulador. | https://www.analog.com/en/
design-center/design-tools-and-calculators/ltspice-simulator.html
[8] Hambley, Allan. Electronics, 2nd Ed., Prentice-Hall, 1999.
[9] Sedra, A.S., Smith, K. Microelectronic Circuits, 5th Ed. McGraw-Hill, 2004.
[10] Website of the ThingSpeak IoT platform. http://www.thingspeak.com/.
[11] Eke, Rustu y Senturk, Ali. Performance Comparison of a Double-Axis Sun Trackingversus Fixed PV System. Solar Energy 86(9): 2665?72, 2012. doi:10.1016/j.solener.2012.06.006.
[12] Arnold Edward, Tresna Dewi y Rusdianasari. The effectiveness of Solar Tracker Use on Solar Panels to The Output of The Generated Electricity Power, IOP Conference Series: Earth and Environmental Science 347, 2019. doi:10.1088/1755-1315/347/1/012130

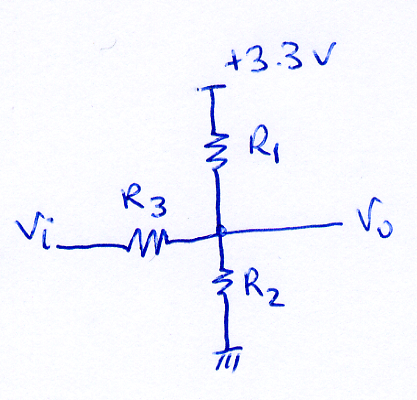
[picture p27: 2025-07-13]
Primera_Parte/Electrónica/Circuito/Offse_positivo/image.png

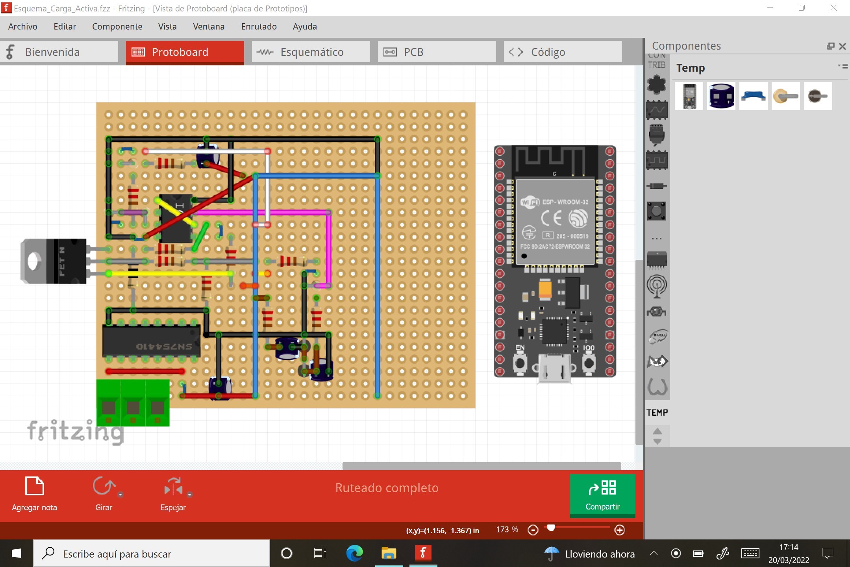
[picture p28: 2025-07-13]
Primera_Parte/Electrónica/Circuito/SharedScreenshot.jpg

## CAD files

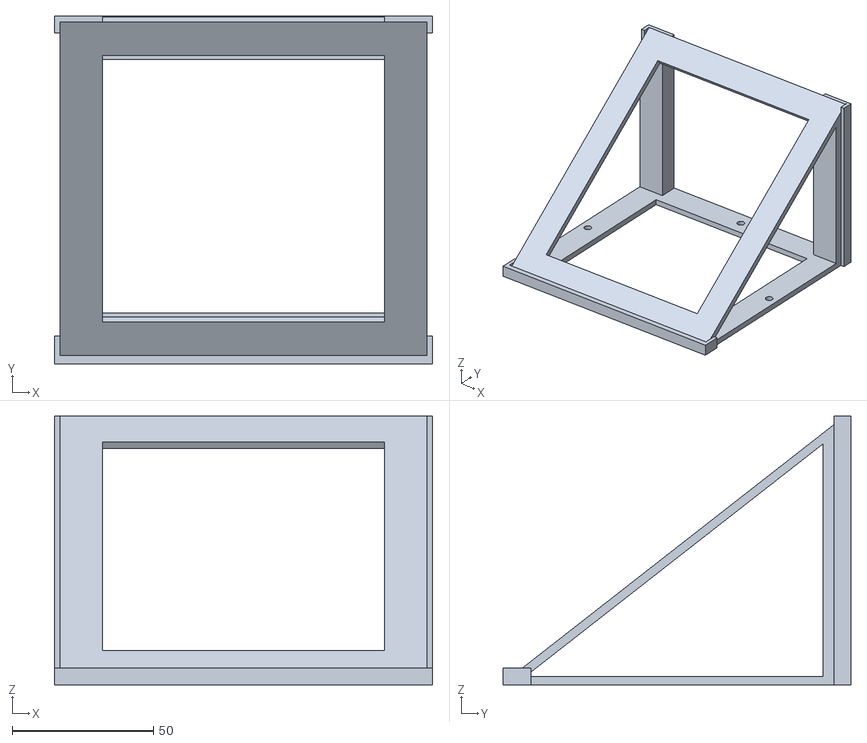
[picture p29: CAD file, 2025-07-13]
Segunda_Parte/Print3D/fija/fijo38.stl
134.0 x 123.3 x 95.4

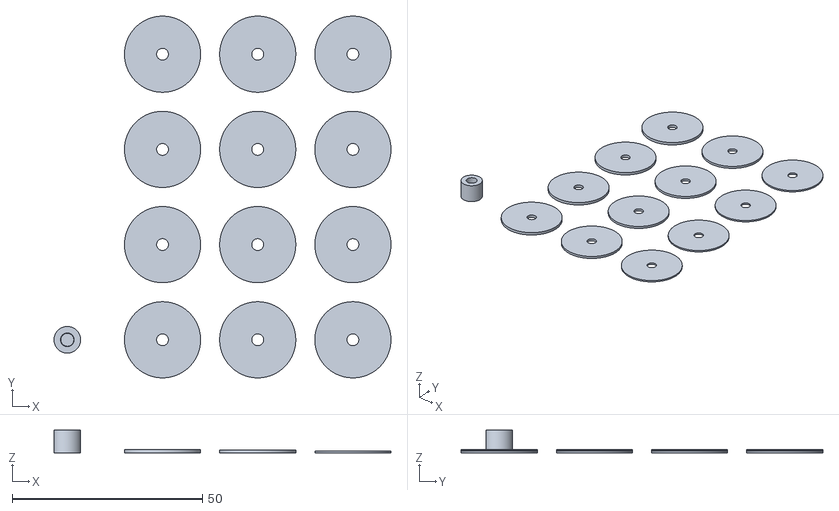
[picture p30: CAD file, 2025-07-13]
Segunda_Parte/Print3D/movil/3D/Arandelas.stl
88.5 x 95.0 x 6.00

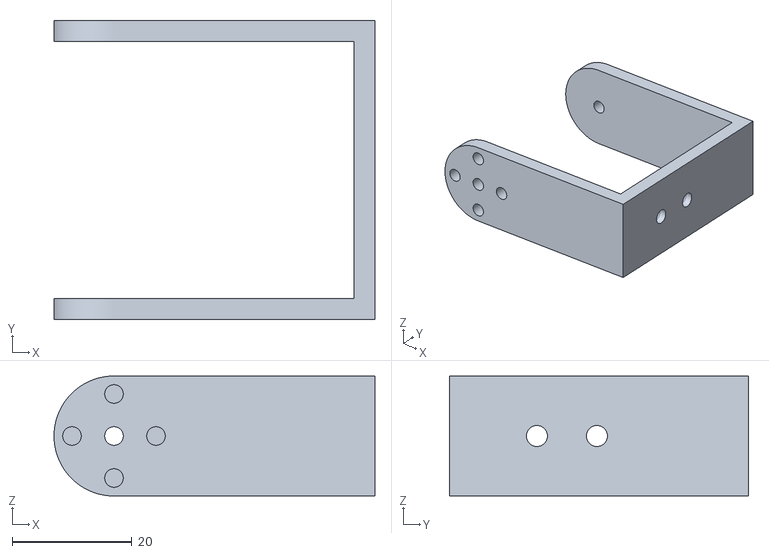
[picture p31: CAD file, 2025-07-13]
Segunda_Parte/Print3D/movil/3D/U.stl
53.5 x 49.9 x 20.0

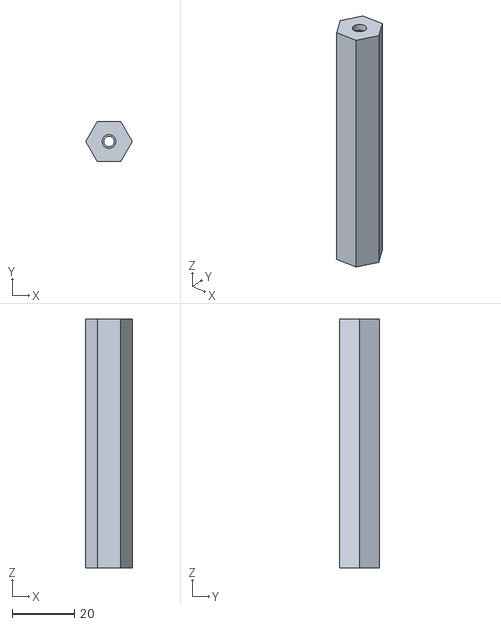
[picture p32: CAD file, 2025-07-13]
Segunda_Parte/Print3D/movil/3D/soportes95.stl
15.0 x 13.0 x 80.0

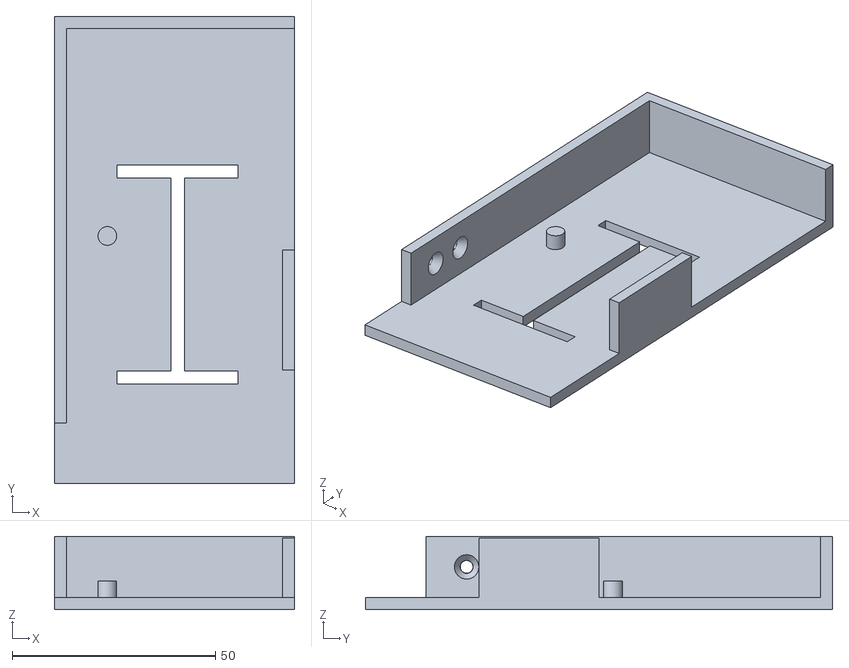
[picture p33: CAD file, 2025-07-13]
Segunda_Parte/Print3D/movil/3D/soporte_brujula.stl
59.0 x 114.9 x 18.0

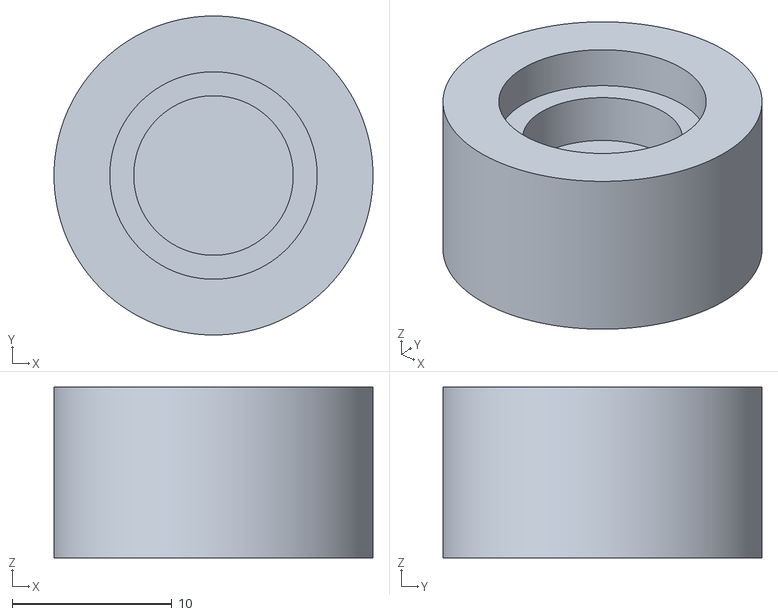
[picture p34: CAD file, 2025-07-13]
Segunda_Parte/Print3D/movil/3D/cojinete_U.stl
20.0 x 20.0 x 10.7

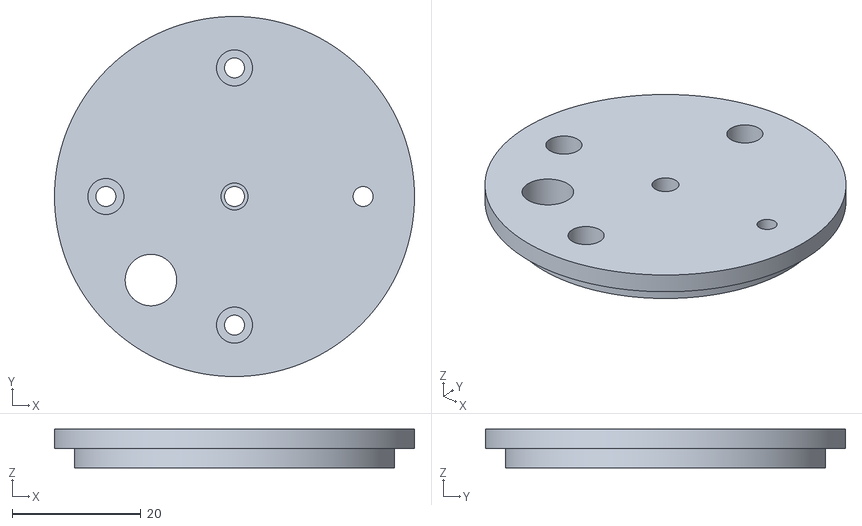
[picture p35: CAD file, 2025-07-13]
Segunda_Parte/Print3D/movil/3D/cojinete_interior_sup.stl
56.0 x 56.0 x 6.00

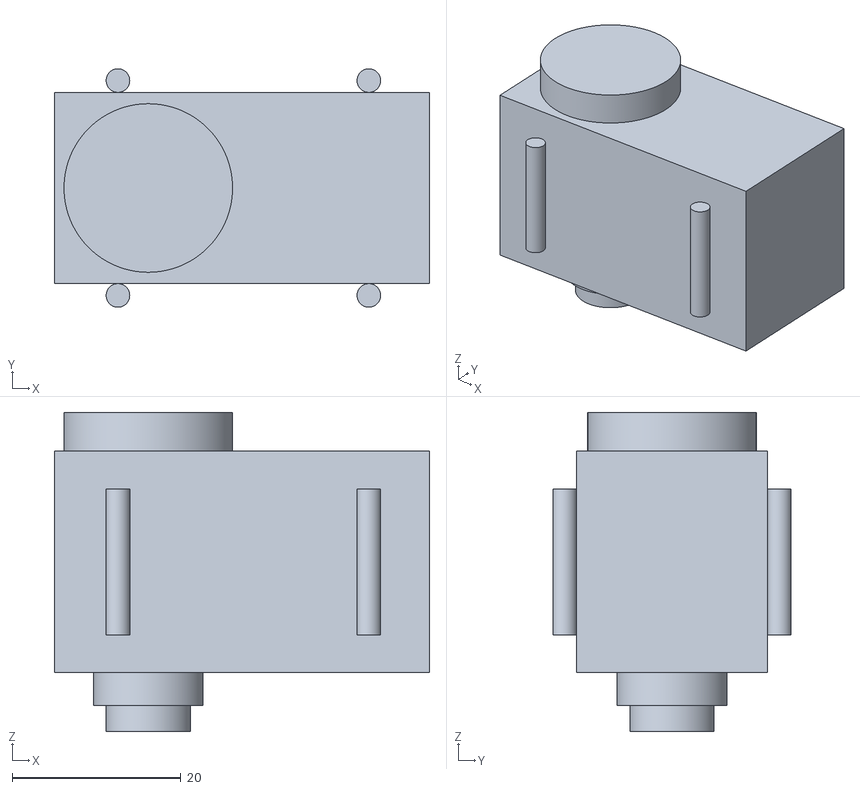
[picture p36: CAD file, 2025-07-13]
Segunda_Parte/Print3D/movil/3D/servo.stl
44.5 x 28.3 x 37.9

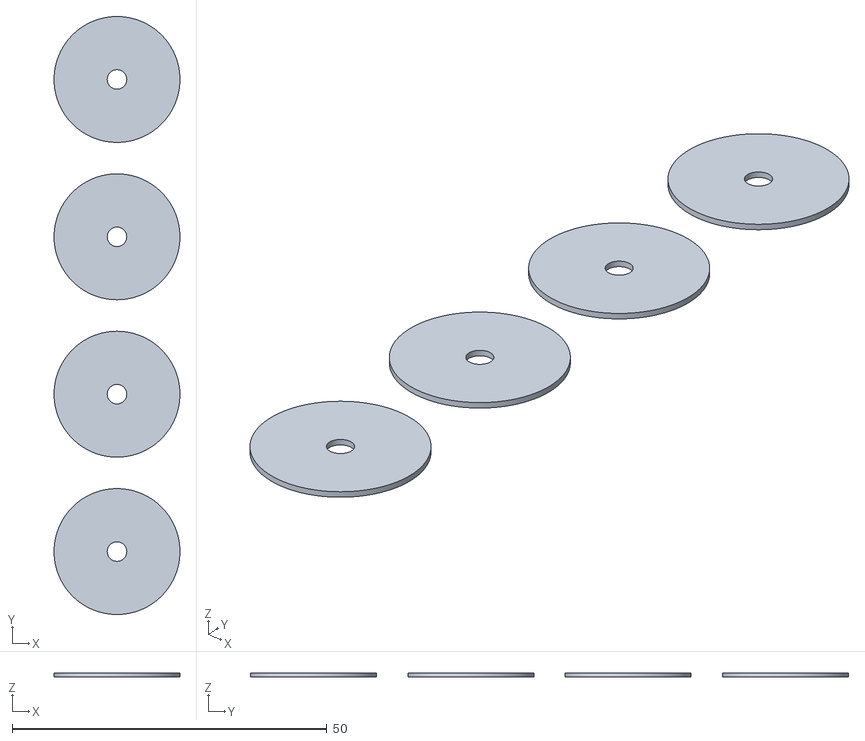
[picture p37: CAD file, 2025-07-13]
Segunda_Parte/Print3D/movil/3D/Arandelas0.7.stl
20.0 x 95.0 x 0.7

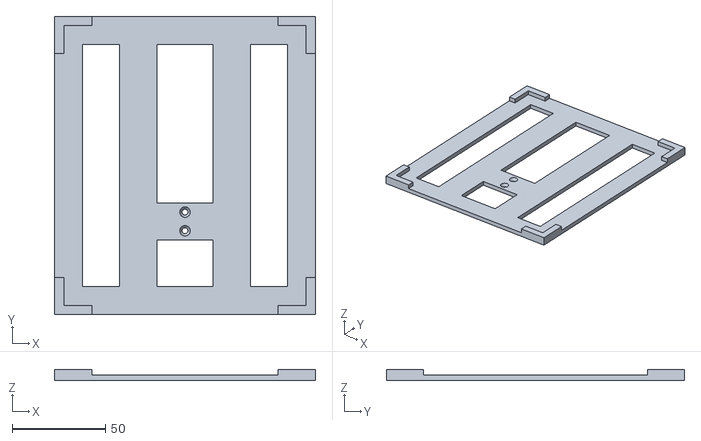
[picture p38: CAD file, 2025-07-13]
Segunda_Parte/Print3D/movil/3D/soporte_panel.stl
140.0 x 160.0 x 6.00

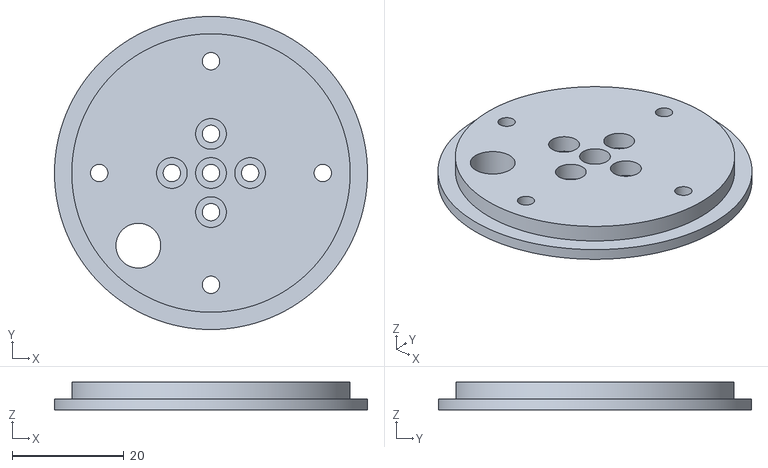
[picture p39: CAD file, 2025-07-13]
Segunda_Parte/Print3D/movil/3D/cojinete_interior_inf.stl
56.0 x 56.0 x 5.00

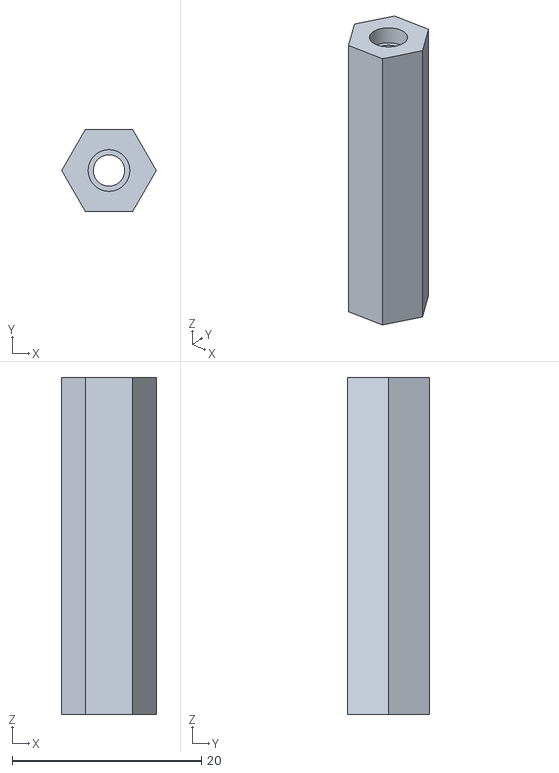
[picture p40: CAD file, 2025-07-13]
Segunda_Parte/Print3D/movil/3D/Soportes.stl
10.0 x 8.66 x 35.6

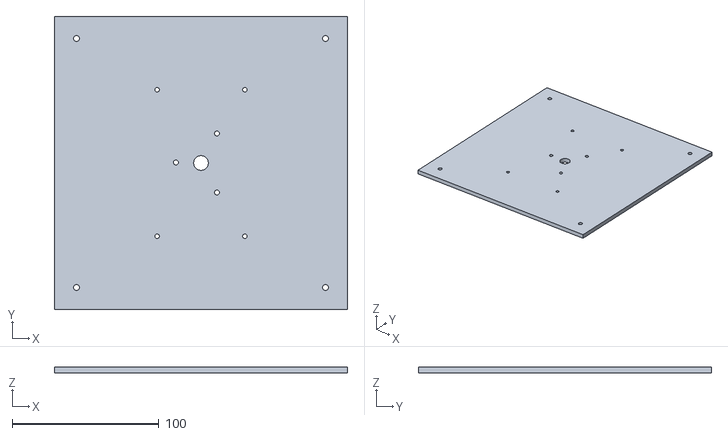
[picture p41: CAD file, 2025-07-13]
Segunda_Parte/Print3D/movil/3D/Base.stl
200.0 x 200.0 x 4.00

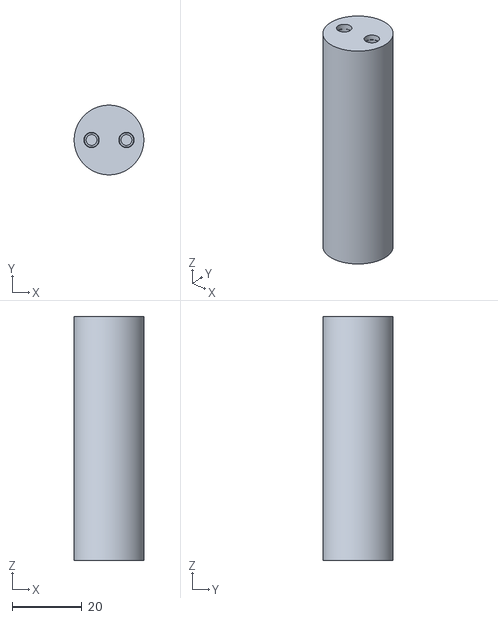
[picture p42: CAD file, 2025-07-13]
Segunda_Parte/Print3D/movil/3D/cilindro.stl
20.0 x 20.0 x 70.0

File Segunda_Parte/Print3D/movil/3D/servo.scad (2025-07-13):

//Servomotor

union(){
cube([44.5,22.7,26.3]);  
    
//cilindros laterales:
    
translate([7.53,-1.4,4.5])
    cylinder(d=2.8,h=17.3,$fn=1000);
translate([37.3,-1.4,4.5])
    cylinder(d=2.8,h=17.3,$fn=1000);
translate([7.53,24.1,4.5])
    cylinder(d=2.8,h=17.3,$fn=1000);
translate([37.3,24.1,4.5])
    cylinder(d=2.8,h=17.3,$fn=1000);
    
//cilindros inferiores:
    
translate([11.13,11.35,-3.9])
    cylinder(d=13,h=3.9,$fn=1000);
translate([11.13,11.35,-7])
    cylinder(d=10,h=3.1,$fn=1000);
    
//cilindro superior:
    
translate([11.13,11.35,26.3])
    cylinder(d=20,h=4.6,$fn=1000);
}

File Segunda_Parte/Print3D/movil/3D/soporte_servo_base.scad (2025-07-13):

//soporte servo base
difference(){
union(){
//cubo principal:
difference(){
    cubo(-2,-3,0,46.5,34.3,8.4);
    cubo(-0.01,2.8,-0.01,44.52,22.7,10);
}
//cubo que contiene tornillos:
difference(){
    cubo(-10,-10,0,54.5,48.5,3);
    cubo(-0.01,2.8,-0.01,44.52,22.7,10);
    //cilindros lamina inferior:
    cilindro(-6,14.5,-0.01,2.5,5); 
    cilindro(22,-6,-0.01,2.5,5); 
    cilindro(22,34.3,-0.01,2.5,5); 
    }
}   
    cubo(0,2.8,-0.1,44.51,22.7,6.9);
    //cilindros lamina superior 1.6mm
    cilindro(7.53,1.4,-0.1,1.6,10);
    cilindro(7.53,26.9,-0.1,1.6,10);
    cilindro(35.35,1.4,-0.1,1.6,10);
    cilindro(35.35,26.9,-0.1,1.6,10);
    //cilindros lamina superior 3mm
    cilindro(7.53,1.4,-0.1,4,4);
    cilindro(7.53,26.9,-0.1,4,4);
    cilindro(35.35,1.4,-0.1,4,4);
    cilindro(35.35,26.9,-0.1,4,4);
}

module cubo(x,y,z,dx,dy,dz){
translate([x,y,z])
    cube([dx,dy,dz]);
}
module cilindro(x,y,z,diam,alt){
    translate([x,y,z])
        cylinder(d=diam,h=alt,$fn=1000);
}

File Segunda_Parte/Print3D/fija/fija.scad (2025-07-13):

//Soporte Fijo:

union(){
    
//Soporte izq  
cube([10,10,41]);
    
//Soporte drch
translate([120,0,0])
    cube([10,10,41]);
    
//Lamina base
    
difference(){
    cube([130,150,3]);
    translate([15,15,-0.01])
        cube([100,120,3.02]);
    translate([65,7.5,0])
        cylinder(d=4,h=10,$fn=100);
    translate([5,60,0])
        cylinder(d=4,h=10,$fn=100);
    translate([125,60,0])
        cylinder(d=4,h=10,$fn=100);
}

//Lamina superior
difference(){
rotate([-16,0,0])
    translate([0,-11.4,39.8])
        cube([130,150,3]);
rotate([-16,0,0])
    translate([10,0,39.7])
        cube([110,130,3.2]);    
}

//Pie
translate([0,145,0])        
    cube([130,5,7]);

//Cuadrado del Hueco
translate([0,0,41])
    cube([130,2.5,2.5]);

//Laminas laterales de sujecion
translate([130,135,0])
    cube([2,15,7]);
translate([-2,135,0])
    cube([2,15,7]);
translate([130,0,37.5])
    cube([2,10,7]);
translate([-2,0,37.5])
    cube([2,10,7]);
}

//----------------------------------------
difference(){
union(){
translate([0,1.85,-2.36])
difference(){
rotate([38,0,0])
    translate([200,0,0])
        cube([130,150,3]);
rotate([38,0,0])
    translate([215,15,-0.1])
        cube([100,120,3.2]);    
}
//Base
translate([200,0,-3])
difference(){
    cube([130,120.34,3]);
    translate([15,15,-0.01])
        cube([100,90,3.02]);
    translate([65,112.84,0])
        cylinder(d=4,h=10,$fn=100);
    translate([5,60,0])
        cylinder(d=4,h=10,$fn=100);
    translate([125,60,0])
        cylinder(d=4,h=10,$fn=100);
}

translate([200.01,110.34,-3])
union(){
//Soporte izq  
cube([14.98,10,95.34]);
//Soporte drch
translate([115,0,0])
    cube([15,10,95.35]);
}

//Laminas laterales de sujecion
//superiores
translate([330,114.34,83.34])
    cube([2,6,9]);
translate([+198.01,114.34,83.34])
    cube([2,6,9]);
//inferiores:
translate([330,-3,-3])
    cube([2,10,6]);
translate([198,-3,-3])
    cube([2,10,6]);

//Cubo sin más
translate([200,-3,-3])
    cube([130,3,6]);
}
//triángulos 1
translate([200,114.53,99])
rotate([-22,0,0])
rotate([0,90,0])
cylinder(r=15,h=15,$fn=3);
//triángulo 2
translate([314.99,114.53,99])
rotate([-22,0,0])
rotate([0,90,0])
cylinder(r=15,h=15.03,$fn=3);
}

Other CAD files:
Segunda_Parte/Print3D/movil/3D/acolpe.stl
Segunda_Parte/Print3D/movil/3D/acople1.stl
Segunda_Parte/Print3D/movil/3D/soporte_serv_2.stl
Segunda_Parte/Print3D/movil/3D/cojinete.stl
Segunda_Parte/Print3D/movil/3D/servo_horizontal.scad
Segunda_Parte/Print3D/fija/fijo38.scad
Segunda_Parte/Print3D/movil/3D/Arandelas.scad
Segunda_Parte/Print3D/movil/3D/Base.scad
Segunda_Parte/Print3D/movil/3D/U.scad
Segunda_Parte/Print3D/movil/3D/acolpe.scad
Segunda_Parte/Print3D/movil/3D/acople1.scad
Segunda_Parte/Print3D/movil/3D/cilindro.scad
Segunda_Parte/Print3D/movil/3D/cojinete.scad
Segunda_Parte/Print3D/movil/3D/cojinete_U.scad
Segunda_Parte/Print3D/movil/3D/cojinete_exterior.scad
Segunda_Parte/Print3D/movil/3D/cojinete_exterior.stl
Segunda_Parte/Print3D/movil/3D/cojinete_interior_inf.scad
Segunda_Parte/Print3D/movil/3D/cojinete_interior_sup.scad
Segunda_Parte/Print3D/movil/3D/completo.scad
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

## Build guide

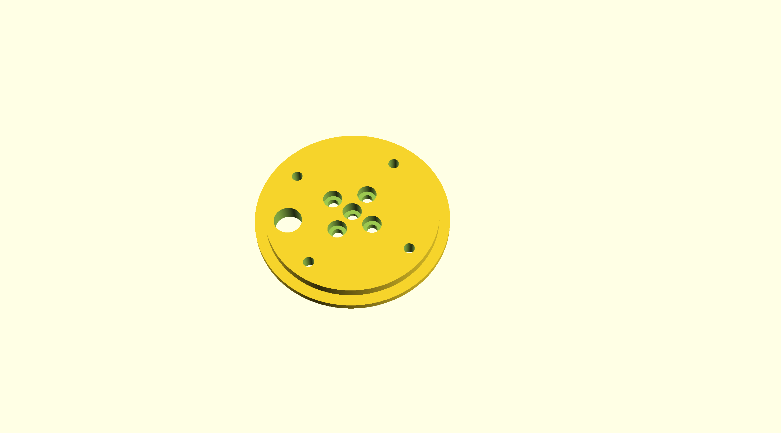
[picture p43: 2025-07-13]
Segunda_Parte/Print3D/movil/3D/cojinete_interior_inf.png

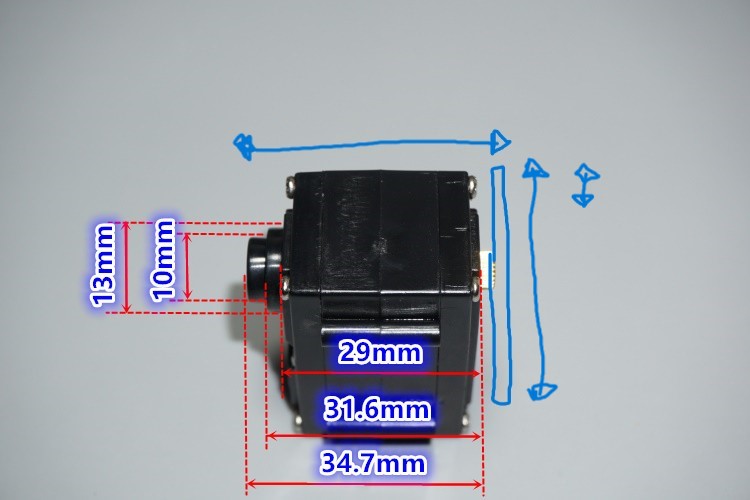
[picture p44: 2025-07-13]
Segunda_Parte/Print3D/movil/medidas/medidas1 (1).jpg

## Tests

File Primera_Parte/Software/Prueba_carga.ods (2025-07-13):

CH3 5,5 V [Panel] |  |  |  | CH3 3,5V [Panel] |  |  |  | CH3 1V [Panel]
V1(fuen)[V] | ADC2(pl1)[V] | R5(osc)[mV] | R2(pl2)[mV] | V1(fuen)[V] | ADC2(pl1)[V] | R5(osc)[mV] | R2(pl2)[mV] | V1(fuen)[V] | ADC2(pl1)[V] | R5(osc)[mV] | R2(pl2)[mV]
3 | 2,673 | 308 | 371 | 3 | 2,21 | 308 | 371 | 3 | 3,248 | 308 | 373
2,85 | 2,613 | 308 | 352 | 2,85 | 2,114 | 308 | 352 | 2,85
2,75 | 2,587 | 308 | 340 | 2,75 | 2,09 | 308 | 340 | 2,75
2,65 | 2,565 | 308 | 327 | 2,65 | 2,056 | 308 | 327 | 2,65
2,5 | 3,091 | 307 | 311 | 2,5 | 3,09 | 308 | 311 | 2,5 | 3,087 | 308 | 311
2,35 | 2,932 | 291 | 292 | 2,35 | 2,923 | 291 | 292 | 2,35 | 2,923 | 290 | 292
2,2 | 2,737 | 273 | 273 | 2,2 | 2,737 | 273 | 273 | 2,2 | 2,736 | 272 | 273
2 | 2,485 | 247 | 248 | 2 | 2,486 | 247 | 248 | 2 | 2,485 | 247 | 248
1,5 | 1,861 | 185 | 186 | 1,5 | 1,861 | 185 | 186 | 1,5 | 1,861 | 185 | 186
1 | 1,233 | 123 | 124 | 1 | 1,234 | 123 | 124 | 1 | 1,233 | 123 | 124
0,5 | 0,608 | 61 | 62 | 0,5 | 0,608 | 61 | 62 | 0,5 | 0,609 | 61 | 61
0,25 | 0,293 | 30 | 30 | 0,25 | 0,294 | 30 | 30 | 0,25 | 0,294 | 30 | 30
0,1 | 0,106 | 11 | 12 | 0,1 | 0,106 | 11 | 12 | 0,1 | 0,106 | 11 | 12
600mA | ->2,42 V en v1

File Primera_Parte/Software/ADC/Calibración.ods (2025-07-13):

Ajuste Corriente
Mediana(mV) | I(A) | lineal | Incer.Lin | Cuadratica | Incert.cuad | cuad con 0 | incer.cuad
331 | 0 | 0,003533565666306 |  | 0,001793673362555 |  | 0,001477543016961 | #¡DIV/0!
346 | 0,0078 | 0,010758013664586 | 37,923252110077 | 0,009136117244513 | 17,1297082629864 | 0,008835079921429 | 13,270255402941
405 | 0,038 | 0,039174175791154 | 3,08993629251055 | 0,037990777673798 | 0,024269279479694 | 0,037746234104892 | 0,667804987126894
466 | 0,0668 | 0,068553597650826 | 2,62514618387126 | 0,0677806098476 | 1,46797881377243 | 0,067589659678333 | 1,18212526696553
527 | 0,097 | 0,097933019510498 | 0,961875784018569 | 0,097526773811274 | 0,543065784818529 | 0,097384521387975 | 0,396413802036095
584 | 0,1256 | 0,125385921903962 | 0,170444343979313 | 0,125282902784946 | 0,252465935552651 | 0,125181730173374 | 0,333017377887
645 | 0,1561 | 0,154765343763634 | 0,855000792034593 | 0,154944593817552 | 0,74017052046626 | 0,154882648671077 | 0,779853509880351
706 | 0,1858 | 0,184144765623306 | 0,890868878737345 | 0,18456261664003 | 0,665975974149537 | 0,184535003304981 | 0,680837833702565
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

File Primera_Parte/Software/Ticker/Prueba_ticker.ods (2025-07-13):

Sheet: Hoja1
SIN CONDENSADOR |  |  |  |  |  |  |  | CON CONDENSADOR 10nF |  |  |  |  |  |  | CON CONDENSADOR 1nF
V_i_Real | Mediana | V_i_teórica | Diferencia(V) | V_I_T_real | Dif(mV) | INC_relativa |  | V_i_Real | Mediana | V_i_teórica | Diferencia(V) | V_I_T_real | Dif(mV) | INC_relativa | V_i_Real | Mediana | V_i_teórica | Diferencia(V) | V_I_T_real | Dif(mV) | INC_relativa
84 | 182 | 57 | 0,027 | 71,76397663 | 12,23602337 | 14,56669449 |  | 75 | 175 | 44 | 0,031 | 58,4571458 | 16,5428542 | 22,05713893 | 83 | 184 | 60 | 0,023 | 75,56592829 | 7,434071706 | 8,956712899
145 | 214 | 114 | 0,031 | 132,5952033 | 12,40479673 | 8,555032227 |  | 146 | 213 | 113 | 0,033 | 130,6942274 | 15,30577256 | 10,48340586 | 146 | 216 | 118 | 0,028 | 136,3971549 | 9,602845064 | 6,57729114
395 | 345 | 353 | 0,042 | 381,6230373 | 13,37696267 | 3,386572827 |  | 395 | 345 | 353 | 0,042 | 381,6230373 | 13,37696267 | 3,386572827 | 395 | 347 | 357 | 0,038 | 385,424989 | 9,575011 | 2,424053418
797 | 556 | 737 | 0,06 | 782,728938 | 14,271062 | 1,79059749 |  | 797 | 555 | 735 | 0,062 | 780,8279622 | 16,17203783 | 2,029113906 | 797 | 557 | 738 | 0,059 | 784,6299138 | 12,37008617 | 1,552081075
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

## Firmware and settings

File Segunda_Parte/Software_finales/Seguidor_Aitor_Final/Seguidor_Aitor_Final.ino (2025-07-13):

/* La finalidad de este programa es estudiar el seguimiento de nuestro set point, en este caso una función triangular para que el setpoint varíe con el tiempo.*/

#include <Arduino.h>
#include <Ticker.h> /* Se incluye la librería Ticker.h */
#include "ThingSpeak.h" /* Se incluye la librería ThingSpeak.h*/
#include "WiFi.h" /* Se incluye la librería WiFi.H*/
#include <PID_v1.h> 
#include "ESP32Time.h" //ESP32Time.h es una biblioteca de tiempos que hace una sincronización con el servidor NTP.
#include "WiFi.h" //WiFi.h es la libreria wifi para conectar el microcontrolador a la red wifi.
#include "UBTech.h" //UBTech.h es una librería que se encarga del control de los servomotores.

#define TESTING   false // Modo de prueba para ver la respuesta a escalones

// Constantes de muestreo
#define N_DATA 5 //11 // Impar

// Constantes y estructura de la función busca_max
#define IMIN 0.0
#define IMAX 700.0 //700.0
#define IINC 100.0
#define MININC 0.75    //Salto mínimo de corriente al buscar (mA)
#define BUSCA_MAX_TIMEOUT 2000   // Tiempo (ms) que busca_max espera para que se alcance el setpoint
#define TEST_PPS  false           // Para hacer la busqueda más lenta cuando se usa la fuente

typedef struct { /* Definimos una nueva estructura de datos similar a los registros de phyton que contiene tres variables diferentes*/
  float I;
  float V;       // Tensión en el punto de máxima potencia
  float P;      // Potencia máxima
  float I_last; // Ultimo valor en el que se pudo fijar el setpoint
  int status; // Indica si el resultado es fiable: 0=OK, -1=Timeout
} PMAX;

// Constantes lazo de control
#define N_DATA_ERR  11 //21 // Número de datos del histórico del error al buscar 
#define USE_PID 0

// Constantes referidas a los Tickers
#define CTRL_TIME 0.005  // Tiempo de ciclo (s) del lazo de control
#define SAMPLE_TIME 0.001 // Tiempo de muestreo
#define DISP_TIME 0.05

const int PIN_PWM = 27; /* PWM*/
const int PIN_SEL = 13; /* Relé*/
const int PIN_ADC2 = 34;	// Corriente
const int PIN_ADC1 = 33;	// Tensión
const int PIN_DAC = 25;  /* [0-255] Digital */

typedef struct {
  float media;
  float mediana;
  float desviacion;
  long tiempo;
} ARRSTAT;

unsigned long channelID = 1687542;
const char* WriteAPIKey = "3QUZEAC5CQG1GPIJ";

WiFiClient cliente; /* Se crea el objeto Cliente*/

Ticker tick_corriente, tick_disp; // Lectura de la tensión en el ADC del micro
float M_e, V_i, I_1, media;
double I;
float V_ref[N_DATA];

Ticker tick_tension;
float V_ref_celula[N_DATA];
float media_celula, M_e_celula, V_celula;

Ticker tick_control;/* Sigue el valor del setpoint */
double dac ; /* Salida DAC. Entrada de la carga activa*/

float err_hist[N_DATA_ERR];   // Array con el historico del error
bool err_fix;                   // Indica si el control ha 'enganchado'
ARRSTAT err_stat;

//Define the aggressive and conservative Tuning Parameters
//double aggKp = 4, aggKi = 0.2, aggKd = 1;
//double consKp = 1, consKi = 0.05, consKd = 0.25;

double aggKp = 4, aggKi = 0.2, aggKd = 1;
//double consKp = 0.25, consKi =1.2, consKd = 0.00;

double consKp = 0.25, consKi =1.0, consKd = 0.0;

double set_point = 0; /* Con esta variable se fija la Intensidad que queremos que demande la carga activa*/

PID pid(&I, &dac, &set_point, consKp, consKi, consKd, P_ON_M, DIRECT);

float i_min;

long ti, tf, tiempo;

//--------------------------------------------------------//
//---------------RELATIVO AL SEGUIDOR SOLAR---------------//
//--------------------------------------------------------//

#define PI 3.14159265358979324 //Número PI
#define Longitud 38.886 //En grados 
#define Latitud -7.007 //En grados. Postitivo al Este del Meridiano_G y negativo al Oeste

//Nombre y contraseña del WiFi:
const char* ssid = "APTest1";
const char* password = "isoTech25";

const char* ntpServer = "pool.ntp.org"; //Servidor NTP
const long gmtOffset_sec = 0; //Desplazamiento GMT * 3600, España +2 pero empleamos el UTC para evitar el horario administrativo.
const int daylightOffset_sec = 0; //Compensación Diurna

typedef struct {
  float Azimutal;
  float Altitud;
}ANGULO;

float Local_Time,Elevacion,Acimutal;
int Year, Day_of_Year, hora;

ESP32Time rtc; //Creamos el objeto objeto

//relativo al movimiento de los servos:
SoftwareSerial ss14(14, 14, false);
UBTech servo(&ss14, &Serial);  // Debug on Serial
int servoCnt = 0;

//----------------------------------------------------------------------------------------------------------------------------------

/*******************************************************************************************
   Función para introducir un nuevo valor y calcular la estadística de un array
*/

ARRSTAT insert_calcula_stat_array(float *data, int ndat, float newdat)
{
  ARRSTAT ret;
  float aux_data[ndat];
  float paso_data;
  int i, j;
  long t_i, t_f;

  t_i = micros();
  /* Realizamos la toma de datos con desplazamientos almacenando los N_DATA últimos elementos. Primero desplazamos los datos */
  for (i = 1; i < ndat; i++) {
    j = i - 1;
    data[j] = data[i];
  }
  data[ndat - 1] = newdat; /* Almacenamos en la última posicion el nuevo valor. */
  /* Se almacenan los datos en un vector auxiliar que posteriormente se ordenará: */
  for (i = 0; i < (ndat); i++) {
    aux_data[i] = data[i];
  }
  for (i = 0; i < (ndat - 1); i++) {
    for (j = i + 1; j < ndat; j++) {
      if (aux_data[j] < aux_data[i]) {
        paso_data = aux_data[j];
        aux_data[j] = aux_data[i];
        aux_data[i] = paso_data;
      }
    }
  }
  float suma = 0;
  for (i = 0; i < (ndat); i++) {
    suma += aux_data[i];
  }
  ret.media = suma / ndat;
  ret.mediana = aux_data[ndat / 2];

  suma = 0;
  for (i = 0; i < (ndat); i++) {
    suma += (aux_data[i] - ret.media) * (aux_data[i] - ret.media);
  }
  ret.desviacion = sqrt(suma / ndat);
  t_f = micros();
  ret.tiempo = t_f - t_i;

  return ret;
}

/******************************************************************************
  Función para muestrear la tensión
*/

void tension() {

  ARRSTAT valores;
  float newdata;

  newdata =analogReadMilliVolts(PIN_ADC1); /* Almacenamos en la última posicion el nuevo valor. */
  valores = insert_calcula_stat_array(V_ref_celula, N_DATA, newdata);

  media_celula = valores.media;
  M_e_celula = valores.mediana;
  V_celula = -0.0000000596427656610408 * M_e_celula * M_e_celula + 0.004911705419677 * M_e_celula - 1.61866365835977;
}

/******************************************************************************
  Función para muestrear la corriente
*/

void intensidad() {

  ARRSTAT valores;
  float newdata;

  ti = micros();
  newdata =analogReadMilliVolts(PIN_ADC2); /* Almacenamos en la última posicion el nuevo valor. */
  valores = insert_calcula_stat_array(V_ref_celula, N_DATA, newdata);

  media = valores.media;
  M_e = valores.mediana;
  I = (-0.00000000586780571462522 * M_e * M_e + 0.000493468763266 * M_e - 0.160901604616591) * 1000; /* Ajuste cuadrático en mA*/
  //V_i = ((M_e / 1000 - 12080 * 9880 * 3.2 / (46770.0 * (12080.0 + 9880.0) + (9880.0 * 12080.0))) * (46770.0 * (12080.0 + 9880.0) + (9880.0 * 12080.0)) / (9880.0 * 46770.0)); /* en Voltios */
  //V_i_1 = ((media / 1000 - 12080 * 9880 * 3.3 / (46770.0 * (12080.0 + 9880.0) + (9880.0 * 12080.0))) * (46770.0 * (12080.0 + 9880.0) + (9880.0 * 12080.0)) / (9880.0 * 46770.0)); /* en Voltios */
  //I = V_i/5.0 * 1000; /* mA */
  //I_1=V_i_1/5.0*1000;
  tf = micros();
  tiempo = tf - ti;
}

/*******************************************************************
 * control_loop - Función del lazo de control de la carga
 */

void control_loop() {

  float err_act, e1_med, e1_stdev, e2_med, e2_stdev;

  err_act = I - set_point;
  err_stat = insert_calcula_stat_array(err_hist, N_DATA_ERR, err_act);
#if USE_PID == 1
  /*if (abs(err_act) < 10)
  { //we're close to setpoint, use conservative tuning parameters
    pid.SetTunings(consKp, consKi, consKd);
  }
  else
  {
    //we're far from setpoint, use aggressive tuning parameters
    pid.SetTunings(aggKp, aggKi, aggKd);
  }*/
  pid.Compute();
#else
  dac = dac - err_act / 600.0 * 255 * 0.1; /* Ajustar este parámetro para que la señal sea más estable I fuente, y no fluctue tanto*/
#endif

  if (dac < 0) dac = 0;
  if (dac > 255) dac = 255;
  dacWrite(PIN_DAC, dac);

  if (set_point >= 60) {
    e1_med=0.02;
    e1_stdev=0.02;
    e2_med=0.03;
    e2_stdev=0.03;
  } else if (set_point >=25) {
    e1_med=0.04;
    e1_stdev=0.04;
    e2_med=0.065;
    e2_stdev=0.065;
  } else if (set_point >=10) {
    e1_med=0.07;
    e1_stdev=0.07;
    e2_med=0.1;
    e2_stdev=0.1;
  } else  {
    e1_med=0.1;
    e1_stdev=0.1;
    e2_med=0.13;
    e2_stdev=0.13;
  }
  
  if (abs(err_stat.media / set_point) < e1_med && err_stat.desviacion / set_point < e1_stdev) {
    err_fix = true;
  } else {
    if (err_fix && abs(err_stat.media / set_point) < e2_med && err_stat.desviacion / set_point < e2_stdev)
      err_fix=true;
    else 
      err_fix = false;
  }
}

/*-------------------------------------------------------------------------------------------------------------------------------
 * busca_max - Función que busca el máximo de potencia en un rango
 * 
 */
 
PMAX busca_max(float mini, float maxi, float inc) {
  PMAX ret;
  float P_max, P_aux, I_aux, V_aux;
  long tini;
  P_max = 0;
  ret.I = 0;
  ret.V = 0;
  ret.P = 0;
  ret.I_last = -1;
  ret.status = 1;

  for (float k = mini; k <= maxi ; k = k + inc) {
    //Serial.print("I_test:");
    //Serial.println(k);
    set_point = k;
    err_fix=false;
    delay(50);
    tini = micros();
    while (!err_fix) {
      if ( (micros() - tini) / 1000.0 > BUSCA_MAX_TIMEOUT) {
        // No hemos conseguido fijar el setpoint en el tiempo fijado
        break;
      }
      delay(10);
    }

    if (err_fix) {    // Si el lazo de control fija el valor, tomamos los datos
      //Serial.println("Error fijado");
      //delay(100);
      I_aux = I;
      V_aux = V_celula;
      P_aux = I_aux * V_aux;
      ret.I_last = k;
      if (P_aux > P_max) {
        ret.I = I_aux;
        ret.V = V_aux;
        ret.P = P_aux;
        if (ret.status >=0) ret.status = 0;
        P_max = P_aux;
      }
    } else {    // Si ha ocurrido un timeout
      if (ret.status>=0) ret.status = -1;
      else ret.status=ret.status-1;
    }
    if (TEST_PPS) delay(1000);
  }
  set_point=0;
  return ret;
}

/*************************************************************************
 * busca_mppt - Busca el punto de máxima potencia de un panel
 */

PMAX busca_mppt(int panel)
{
  PMAX ret,ret_max;
  float imin,imax,iinc;
  digitalWrite(PIN_SEL, panel);
  delay(100);

  imin=IMIN;
  imax=IMAX;
  iinc=IINC;

  Serial.printf("\nBuscando MPPT en panel %d\n", panel);

  ret_max.P=-1;
  while (iinc>MININC) {
    Serial.printf("\nIMIN: %.2f mA, IMAX: %.2f mA, IINC: %.2f mA\n",imin, imax, iinc);
    
    ret = busca_max(imin, imax, iinc);
    Serial.print("Stat:");
    Serial.print(ret.status);
    Serial.print(",");
    Serial.print("I_last:");
    Serial.print(ret.I_last);
    Serial.print(",");
    Serial.print("Int_MAX:");
    Serial.print(ret.I);
    Serial.print(",");
    Serial.print(" Vol_max:");
    Serial.print(ret.V);
    Serial.print(",");
    Serial.print("Pot_max:");
    Serial.println(ret.P);
    imin=ret.I-iinc*1.1;
    imax=ret.I+iinc*1.1;
    iinc=iinc/2;
    if (imin < IMIN) imin=IMIN;
    if (imax > IMAX) imax=IMAX;

    if (ret.P > ret_max.P) {
      ret_max=ret;
      Serial.printf("Nuevo MPPT: %.0f mW\n",ret_max.P);
    } else {
      Serial.println("Warning: el nuevo muestreo no ha encontrado MPPT");
    } 
  } 

  Serial.printf("\nPanel: %d\nPmax: %.0f mW\n\n",panel,ret_max.P);
  
  return ret_max;
}

//--------------------------------------------------------//
//---------------RELATIVO AL SEGUIDOR SOLAR---------------//
//--------------------------------------------------------//

ANGULO calculo_angular(int Year, float Local_Time, int hora, int Day_of_Year){
  ANGULO ret;
  float x, EqTime, Declinacion, Time_offset, TimeSolar, Angulo_horario, Alt, Alt_grados, Acim, Acim_grados,Declinacion_grados;
  int dias_year;
  
  //Veamos si el año es bisiesto o no:
  if (Year % 4 == 0 && Year % 100 != 0 || Year % 400 == 0)
    dias_year = 366; //El año es bisiesto!
  else
    dias_year = 365; //No bisiesto!
    
  //Una vez sabemos si el año es bisiesto o no, podemos proceder a calcular el resto de variables. Año fraccionado en Radianes:
  x = 2*PI/dias_year * (Day_of_Year - 1 + (hora - 12)/24);
  //Con x, podemos obtener la ecuacion del tiempo (en minutos) y la declinación (en radianes):
  EqTime = 229.18 * (0.000075 + 0.001868 * cos(x) - 0.032077 * sin(x) - 0.014615 * cos(2*x)-0.040849 * sin(2*x));
  Declinacion =  0.006918 - 0.399912 * cos(x) + 0.070257 * sin(x) - 0.006758 * cos(2*x) + 0.000907 * sin(2*x) - 0.002697 * cos(3*x) + 0.00148 * sin(3*x);
  Declinacion_grados = Declinacion * 360 / (2*PI);
  //Para calcular el tiempo solar necesitamos dos expresiones. La primera asociada al desplazamiento temporal (en minutos):
  Time_offset = EqTime + 4 * Latitud;
  TimeSolar = Local_Time + Time_offset / 60; //Tiempo solar en horas
  Angulo_horario = 15 * (TimeSolar - 12);  //En grados
  Alt = asin(sin(Declinacion) * sin(Longitud*2*PI/360) + cos(Longitud*2*PI/360) * cos(Declinacion) * cos(Angulo_horario*2*PI/360)); //En radianes
  Alt_grados = Alt * 360 / (2*PI);
  Acim = asin((cos(Declinacion) * sin(Angulo_horario*2*PI / 360)) / cos(Alt)); // En radianes
  Acim_grados = Acim *360 / (2*PI); 
  ret.Altitud  = Alt_grados; 
  ret.Azimutal = Acim_grados; 
  Serial.println(ret.Altitud);
  Serial.println(ret.Azimutal);
  return ret;
}  

void movimiento(float Elevacion, float Acimutal){
  int OffSet_azimut = +9;
  int OffSet_elevacion = 0;
  if (Elevacion >= 0){
      servo.move(1, (120 + Acimutal + OffSet_azimut), 50);
      servo.move(2, (120 + Elevacion + OffSet_elevacion), 50);
  }
}

//------------------------------------------------------------------------------------------------------------------------------------
void display_msg() {
  //Serial.print("t_us:");
 // Serial.print(tiempo);
  //Serial.print(",");
  //Serial.print("Mediana: ");
  //Serial.print(M_e);
  //Serial.print(" Mediana celula:");
  //Serial.print(M_e_celula);
  //Serial.print(" I actual: ");
  //Serial.print(I);
  //Serial.print(" T celula: ");
  //Serial.print(V_celula);
  //Serial.print(" DAC actual: ");
  //Serial.println(dac);

  //Serial.println("------- Valores control -------------");

  /*Serial.print("ERR_Media:");
  Serial.print(err_stat.media);
  Serial.print(",");
  Serial.print("ERR_Deviacion:");
  Serial.print(err_stat.desviacion);
  Serial.print(",");
  Serial.print("ERR_Tiempo:");
  Serial.print(err_stat.tiempo);
  Serial.print(",");*/
  Serial.print("Setpoint:");
  Serial.print(set_point);
  Serial.print(",");
  Serial.print("I:");
  Serial.print(I);
  Serial.print(",");
  Serial.print("V*10:");
  Serial.print(V_celula*10);
  Serial.print(",");
  Serial.print("ERROR:");
  Serial.print(set_point-I);
  Serial.print(",");  
  Serial.print("ERR_FIX:");
  Serial.print(err_fix*50);
  Serial.print(",");  
  Serial.print("DAC:");
  Serial.println(dac);



  //Serial.println("------------------------");
}

void setup() {
  //MONITOR SERIE:
  Serial.begin(115200);
  err_fix = false;
  pid.SetMode(AUTOMATIC);
  pid.SetSampleTime(CTRL_TIME * 1000);

#if TESTING == false

  //INICIA CONEXIÓN WiFi:
  WiFi.begin(ssid,password); /* Nos conectamos al router WiFi*/
  while (WiFi.status() != WL_CONNECTED){
    delay(500);
    Serial.print(".");
  }
  Serial.println("Wifi conectado!");
  ThingSpeak.begin(cliente); /* Inicializamos servidor ThingSpeak */

#endif

  Serial.println("");
  Serial.println("Configurando ADCs e I/O");
  
  analogReadResolution(11);
  analogSetAttenuation(ADC_6db);
  pinMode(PIN_SEL, OUTPUT);
  digitalWrite(PIN_SEL, LOW); /* Entrada izq=3.3=fijo, Drch=0=movil*/
  pinMode(PIN_PWM, OUTPUT);
  analogWrite(PIN_PWM, 127);

  // Arrancamos Tickers

  tick_tension.attach(SAMPLE_TIME, tension);
  tick_corriente.attach(SAMPLE_TIME, intensidad);
  tick_control.attach(CTRL_TIME, control_loop);
#if TESTING == true
  tick_disp.attach(DISP_TIME, display_msg);
#endif

//--------------------------------------------------------//
//---------------RELATIVO AL SEGUIDOR SOLAR---------------//
//--------------------------------------------------------//

  //CONFIGURACIÓN DE LA HORA:
  configTime(gmtOffset_sec,daylightOffset_sec,ntpServer);

  //Esperamos a que el tiempo se configure bien
  struct tm timeinfo;
  getLocalTime(&timeinfo,100000);
  Serial.println(&timeinfo, "%A, %B %d %Y %H:%M:%S");

  //RELATIVO AL MOVIMIENTO DE LOS SERVOS:
  servo.init(2);
  servo.setDebug(true);  // Do not view servo detction here
  servo.begin();
  servo.setDebug(true);
  Serial.println(F("\n\nAvailable servo:"));
  servoCnt = 0;
  for (int id = 1; id <= 2; id++) {
    if (servo.exists(id)) {
      Serial.print(F("Servo ID="));
      Serial.print(id);
      Serial.println(F(" is avalable."));
      servo.setLedOff(id); // turn the led off (default on when power on)
      servoCnt++;
    }
  }
  Serial.println();
  if (servoCnt > 0) {
    Serial.print(servoCnt);
  } else {
    Serial.print(F("No "));
  }
  Serial.println(F(" servo detected."));
}

void loop() {
  
  //--------------------------------------------------------//
  //---------------RELATIVO AL SEGUIDOR SOLAR---------------//
  //--------------------------------------------------------// 
  
  ANGULO retu;
  hora = rtc.getHour(true);
  Year = rtc.getYear();
  Day_of_Year = rtc.getDayofYear() + 1; //[0-365] Hay que sumarle 1 porque inicia en el 0.
  Local_Time = rtc.getHour(true) + rtc.getMinute()/60.0 + rtc.getSecond()/3600.0; //En horas
  retu = calculo_angular(Year,Local_Time,hora,Day_of_Year);
  Elevacion = retu.Altitud;
  Acimutal  = retu.Azimutal;
  movimiento(Elevacion,Acimutal);
  
  //--------------------------------------------------------//
  //---------------RELATIVO A LA CARGA ACTIVA---------------//
  //--------------------------------------------------------// 
  
  PMAX ret;
  long tini,tfin;
  tini=millis(); 

#if TESTING == true
 
  digitalWrite(PIN_SEL,LOW);
  delay(100);
  set_point=5;
  delay(4000);
  set_point=10;
  delay(4000);
  set_point=20;
  delay(4000);
  set_point=30;
  delay(4000);
  set_point=40;
  delay(4000);
  set_point=50;
  delay(4000);
  set_point=60;
  
#else
  
  Serial.println("");
  Serial.println("Nueva iteración de búsqueda");

  //--------------------------------------------------------//
  //---------------------RELATIVO A IOT---------------------//
  //--------------------------------------------------------// 

  // Primer panel 
  
  ret=busca_mppt(LOW);
  
  ThingSpeak.setField(1,ret.I); // Se crea el campo
  ThingSpeak.setField(2,ret.V);
  ThingSpeak.setField(3,ret.P);
  
  // El otro panel
  
  ret=busca_mppt(HIGH);
 
  ThingSpeak.setField(4,ret.I);
  ThingSpeak.setField(5,ret.V);
  ThingSpeak.setField(6,ret.P);
  
  // Variables angulares
  
  ThingSpeak.setField(7,retu.Altitud);  
  ThingSpeak.setField(8,retu.Azimutal);

  //Subimos los datos a ThingSpeak
  
  ThingSpeak.writeFields(1687542,"3QUZEAC5CQG1GPIJ"); //Subimos los datos cada 2 min
  Serial.println("Datos subidos a ThingSpeak");

 #endif

 tfin=millis();
 int dela;

 dela=15000-(tfin-tini);
 if (dela < 0) dela=0;
 delay(dela);  
}

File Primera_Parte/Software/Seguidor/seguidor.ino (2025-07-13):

/* La finalidad de este programa es estudiar el seguimiento de nuestro set point, en este caso una función triangular para que el setpoint varíe con el tiempo.*/
#include <Ticker.h> /* Se incluye la librería Ticker.h */
#include "ThingSpeak.h" /* Se incluye la librería ThingSpeak.h*/
#include "WiFi.h" /* Se incluye la librería WiFi.H*/
#define N_DATA 11 // Impar
#define IMIN 0.0
#define IMAX 700.0
#define IINC1 100.0
#define IINC2 25.0
#define IINC3 5.0

const char* ssid = "BocataDeChorizo";
const char* pasword = "DiosNoExiste";

unsigned long channelID = 1687542;
const char* WriteAPIKey = "3QUZEAC5CQG1GPIJ";

WiFiClient cliente; /* Se crea el objeto Cliente*/

const int PIN_PWM=27; /* PWM*/
const int PIN_SEL=13; /* Relé*/

Ticker ADC, Tick_dis; // Lectura de la tensión en el ADC del micro 
const int PIN_ADC2 = 34;
float M_e,V_i,I,I_1,cuenta,media;
float V_ref[N_DATA];

Ticker tension_celula;
const int PIN_ADC1=33;
float V_ref_celula[N_DATA];
float media_celula, M_e_celula, V_celula;

Ticker control;/* Suigue el valor del setpoint */
const int PIN_DAC = 25;  /* [0-255] Digital */
float dac ; /* Salida DAC. Entrada de la carga activa*/
//------------------------------------------------------------------------------------------------------------------------------
typedef struct { /* Definimos una nueva estructura de datos similar a los registros de phyton que contiene tres variables diferentes*/
float I;
float V;
float P;  
}PMAX;

float set_point=0; /* Con esta variable se fija la Intensidad que queremos que demande la carga activa*/
float i_min;
//----------------------------------------------------------------------------------------------------------------------------------
void celula_fotovoltaica() {
  float Aux_celula[N_DATA];
  float paso_celula;
  int i,j;
  /* Realizamos la toma de datos con desplazamientos almacenando los N_DATA últimos elementos. Primero desplazamos los datos */
  for (i = 1; i < N_DATA; i++) {
    j = i - 1;
    V_ref_celula[j] = V_ref_celula[i];
  }
  V_ref_celula[N_DATA - 1] = analogReadMilliVolts(PIN_ADC1); /* Almacenamos en la última posicion el nuevo valor. */
  /* Se almacenan los datos en un vector auxiliar que posteriormente se ordenará: */
  for (i = 0; i < (N_DATA); i++) {
    Aux_celula[i] = V_ref_celula[i];
  }
  for (i = 0; i < (N_DATA - 1); i++) {
    for (j = i + 1; j < N_DATA; j++) {
      if (Aux_celula[j] < Aux_celula[i]) {
        paso_celula = Aux_celula[j];
        Aux_celula[j] = Aux_celula[i];
        Aux_celula[i] = paso_celula;
      }
    }
  }
  float suma=0;
  for (i = 0; i<(N_DATA); i++) {
    suma+=Aux_celula[i];
  }
  media_celula=suma/N_DATA;
  M_e_celula = Aux_celula[N_DATA / 2];
  V_celula=-0.0000000596427656610408 *M_e_celula*M_e_celula+0.004911705419677*M_e_celula-1.61866365835977;
}

void intensidad() {
  float Aux[N_DATA];
  float paso;
  int i,j;
  /* Realizamos la toma de datos con desplazamientos almacenando los N_DATA últimos elementos. Primero desplazamos los datos */
  long ti,tf;
  ti = micros();
  for (i = 1; i < N_DATA; i++) {
    j = i - 1;
    V_ref[j] = V_ref[i];
  }
  V_ref[N_DATA - 1] = analogReadMilliVolts(PIN_ADC2); /* Almacenamos en la última posicion el nuevo valor. */
  /* Se almacenan los datos en un vector auxiliar que posteriormente se ordenará: */
  for (i = 0; i < (N_DATA); i++) {
    Aux[i] = V_ref[i];
  }
  for (i = 0; i < (N_DATA - 1); i++) {
    for (j = i + 1; j < N_DATA; j++) {
      if (Aux[j] < Aux[i]) {
        paso = Aux[j];
        Aux[j] = Aux[i];
        Aux[i] = paso;
      }
    }
  }
  float suma=0;
  for (i = 0; i<(N_DATA); i++) {
    suma+=Aux[i];
  }
  media=suma/N_DATA;
  M_e = Aux[N_DATA / 2]; /* Se obtiene el valor de la mediana y se calcula la tensión en V_i de la salida de la carga activa.*/
  I= (-0.00000000586780571462522 * M_e * M_e + 0.000493468763266 * M_e - 0.160901604616591)*1000; /* Ajuste cuadrático en mA*/
  //V_i = ((M_e / 1000 - 12080 * 9880 * 3.2 / (46770.0 * (12080.0 + 9880.0) + (9880.0 * 12080.0))) * (46770.0 * (12080.0 + 9880.0) + (9880.0 * 12080.0)) / (9880.0 * 46770.0)); /* en Voltios */
  //V_i_1 = ((media / 1000 - 12080 * 9880 * 3.3 / (46770.0 * (12080.0 + 9880.0) + (9880.0 * 12080.0))) * (46770.0 * (12080.0 + 9880.0) + (9880.0 * 12080.0)) / (9880.0 * 46770.0)); /* en Voltios */
  //I = V_i/5.0 * 1000; /* mA */
  //I_1=V_i_1/5.0*1000;
  tf = micros();
  cuenta=tf-ti;
}

void ajuste_setpoint() {
  dac = dac - (I - set_point)/600.0 * 255 * 0.1; /* Ajustar este parámetro para que la señal sea más estable I fuente, y no fluctue tanto*/
  if (dac < 0) dac = 0;
  if (dac > 255) dac = 255;
  dacWrite(PIN_DAC, dac);
}

//-------------------------------------------------------------------------------------------------------------------------------
PMAX busca_max(float mini,float maxi,float inc){
  PMAX ret;
  float P_max, P_aux;
  for (float k=mini; k <= maxi ; k=k+inc){ 
    set_point=k;
    while ((I-set_point) > 3){
      Serial.print(" 1_W ");
      Serial.print(" Set_point: ");
      Serial.print(set_point);
      Serial.print(" I: ");
      Serial.println(I);
      delay(50);//0,05 Segundos
      if (set_point >= maxi){
      delay(200);
      break;
      }
    }
    P_max=I/1000.0*V_celula;
    Serial.print(" P_max: ");
    Serial.print(P_max);
    if (P_max > P_aux){
      Serial.print("Hi");;
      while ((I-set_point) > 2){
        delay(50);
        if (set_point >= maxi){
          break;
        }
      }
      ret.I=I/1000.0;
      ret.V=V_celula;
      ret.P=ret.I*ret.V;
    } else{
      break;
      }
   P_aux=P_max;
  }
  return ret;
}

//------------------------------------------------------------------------------------------------------------------------------------
void display_msg(){
  //Serial.print("Tiempo: ");
  //Serial.print(cuenta);
  //Serial.print("Mediana: ");
  //Serial.print(M_e);
  //Serial.print(" Mediana celula:");
  //Serial.print(M_e_celula);
  //Serial.print(" I actual: ");
  //Serial.print(I);
  //Serial.print(" T celula: ");
  //Serial.print(V_celula);
  //Serial.print(" DAC actual: ");
  //Serial.println(dac);
}

void setup() {
  Serial.begin(115200);
  //WiFi.begin("BocataDeChorizo","DiosNoExiste"); /* Nos conectamos al router WiFi*/
  //while (WiFi.status() != WL_CONNECTED){
  //  delay(500);
  //  Serial.print(".");   
  //}
  //Serial.println("Wifi conectado!");
  //ThingSpeak.begin(cliente); /* Inicializamos servidor ThingSpeak */
  
  analogReadResolution(11);
  analogSetAttenuation(ADC_6db);
  pinMode(PIN_SEL,OUTPUT);
  digitalWrite(PIN_SEL,LOW);/* Entrada izq=3.3=fijo, Drch=0=movil*/
  pinMode(PIN_PWM,OUTPUT);
  tension_celula.attach(0.05,celula_fotovoltaica);
  ADC.attach(0.05, intensidad);
  control.attach(0.05, ajuste_setpoint);
  //Tick_dis.attach(1.0,display_msg);
  analogWrite(PIN_PWM,127);
}
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

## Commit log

2025-07-13 Primer commit
    [Arandelas.scad, Arandelas.stl, Arandelas0.7.stl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]
2025-07-13 Ignorar carpeta Segunda_Parte/Resultados
    [Comparar células 0y1.xlsx, Ultima.xlsx, Uno.xlsx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]
